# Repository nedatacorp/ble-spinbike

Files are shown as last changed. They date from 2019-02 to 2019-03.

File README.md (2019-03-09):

# ble-spinbike
This project is about building a "smart" spinbike from a low-cost, standard spinbike, thus saving a lot of money and having a lot of fun building it and riding it. The result is a spinbike that will work with popular on-line virtual exercise applications, such as Zwift and Bkool. This project was developed specifically using Zwift, but should work with any other product that supports standard Bluetooth GATT technology.

Spinbike is a Javascript node.js application that runs on a Raspberry Pi 3 B+. It gathers data from sensors attached to a spinbike and feeds the data over a bluetooth LE connection to client applications, using the Bluetooth LE (Low Energy) GATT protocol. The GATT protocol is recognized by all major online virtual exercise platforms.

This project provides three of the main exercise bike services: Cadence/Speed, Power and Control. Online apps generally require at least Cadence/Speed or Power in order to allow you to connect and participate. Control is optional, and generally involves feeding the bike information about wind speed, road resistance and grade so it can adjust the effort required by the rider. You can build as much or as little as you want. 

Here is the fritzing diagram for the Raspberry PI, sensors and controllers:

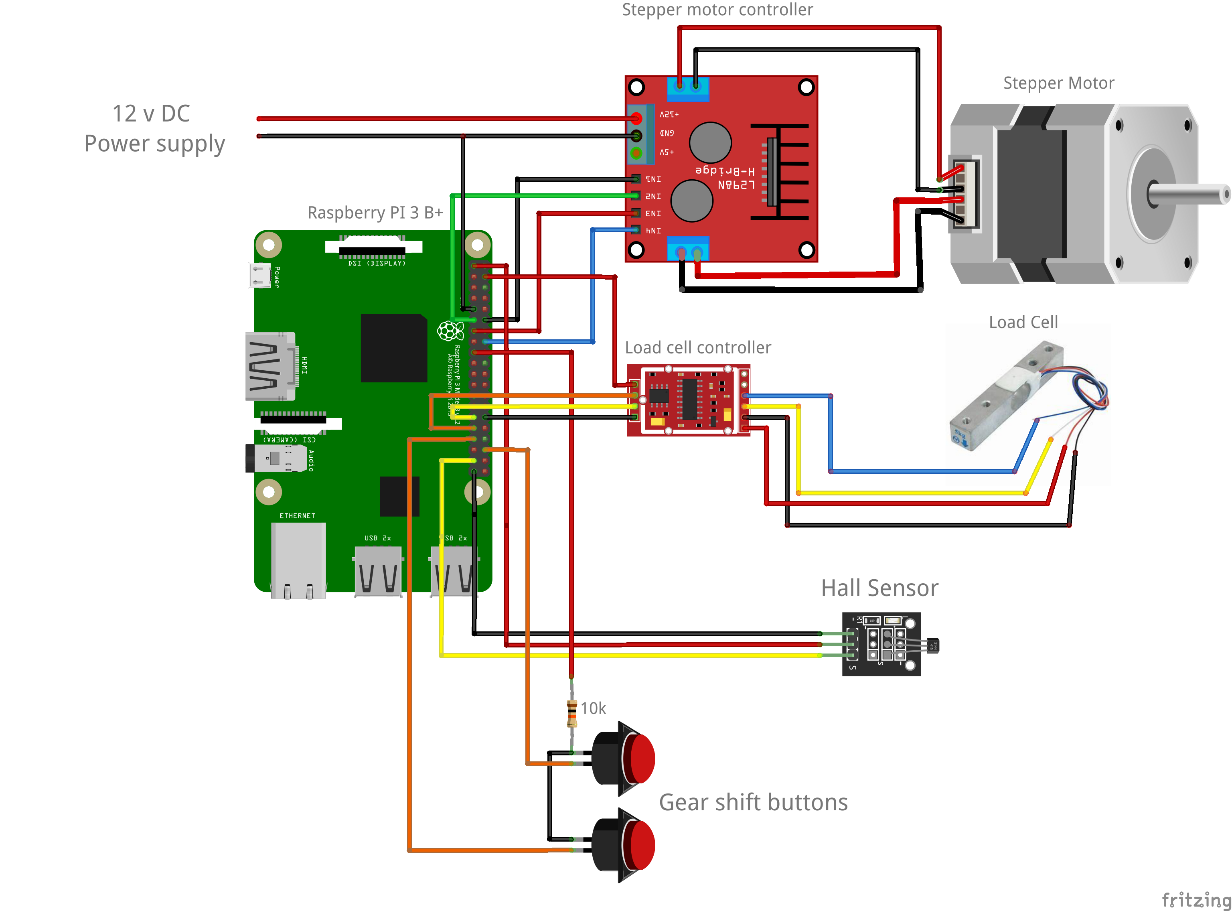
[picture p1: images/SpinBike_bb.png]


I chose a Yosuda spin bike for this project:

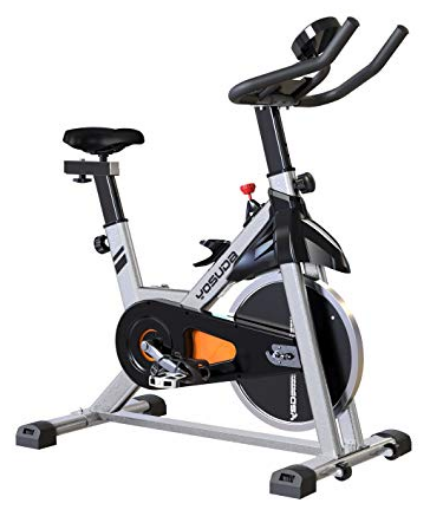
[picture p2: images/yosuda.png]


It has three attributes that make it nice for installing the sensors we need, and the optional stepper motor for controlling resistance:

* A magnet on the main drive pulley and a hole just below the crankshaft where a Hall sensor can be mounted for measuring cadence.
* A steering head that is extended below the main frame, providing a perfect location to mount the load cell for measuring the force on the wool brake pad from the front wheel. 
* A flat-sided steering head and a tension shaft located in just the right spot for making it easy to mount the optional stepper motor, which replaces the tension knob and allows for computerized resistance control.

## System Diagram

This is how the software pieces fit together:

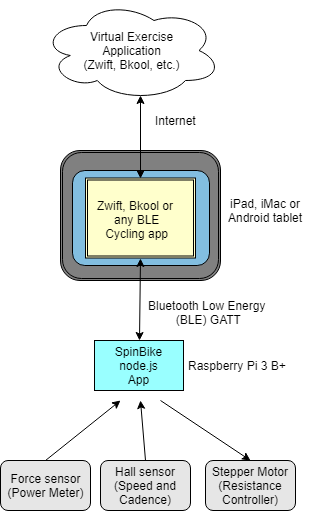
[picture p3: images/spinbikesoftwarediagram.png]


Although most cycling applications support ANT as well as Bluetooth LE (hereafter referred to as "BLE"), I chose Bluetooth for a couple reasons:

* We're using a spinbike, which is indoors and stationary. We don't need the robustness of ANT that's better suited for outdoors and real bicycles. 
* We can use conventional, built-in bluetooth devices, thus avoiding the added cost of ANT dongles.

The major components of this project are the spin bike, a tablet (iPad or Android) or smart phone (iphone or Android), a Raspberry Pi, and about $50 in sensors/misc. hardware. You can also use a standard Mac or PC in place of the tablet, but a tablet works better because you can mount it on the handlebars. You do need either a smart phone/tablet or computer that supports Bluetooth 4.0 and thus Bluetooth low energy. 

Although you don't need the latest computer equipment for this, you also can't use antiques. I specify the Raspberry Pi 3 B+ because it has built-in bluetooth. Old iPads won't run the Zwift app. On the other hand, I had no problem using a 2007 iMac. You'll have to experiment.

For situations where you don't have a tablet that has bluetooth LE capability, you can run a bridge application such as "Zwift Companion" on your smart phone that will communicate between your spin bike (our Raspberry Pi computer, actually) and the full-blown Zwift application running on your PC or Mac.

## Parts List

|Part |Description |Price |Link |
|:--- |:---|:-----|:---|
|L-001A |Yosuda Spin Bike |$250  |https://www.amazon.com/dp/B07D528W98/ref=emc_b_5_t|
|RaspBerry Pi 3 B+|Raspberry Pi|$50|https://www.amazon.com/CanaKit-Raspberry-Power-Supply-Listed/dp/B07BC6WH7V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|
|KY-003 Hall Sensor|Hall Sensor with controller board|$3|https://www.amazon.com/SODIAL-magnetic-sensor-module-Arduino/dp/B077RSV94Z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|
|Flex Coupling|For connecting stepper motor to resistance shaft|$8|https://www.amazon.com/gp/product/B01HBPHSII/ref=ppx_yo_dt_b_asin_title_o07__o00_s00?ie=UTF8&psc=1|
|17HS13-0404S1|Nema 17 stepper motor|$11|https://www.amazon.com/gp/product/B00PNEQ9T4/ref=ppx_yo_dt_b_asin_title_o02__o00_s00?ie=UTF8&psc=1|
|Stepper motor bracket|For attaching stepper motor to steering post|$6.50|https://www.amazon.com/gp/product/B00Q6F51C0/ref=ppx_yo_dt_b_asin_title_o03__o00_s00?ie=UTF8&psc=1|
|L298N|Stepper motor controller|$7|https://www.amazon.com/gp/product/B00CAG6GX2/ref=ppx_yo_dt_b_asin_title_o04__o00_s00?ie=UTF8&psc=1|
|Hx711|Load Cell|$13|https://www.amazon.com/gp/product/B075317R45/ref=ppx_yo_dt_b_asin_title_o05__o00_s00?ie=UTF8&psc=1|
|28 awg 3-conductor wire|3 conductor with ground|$12|https://www.amazon.com/StrivedayTM-3-core-Control-Shielded-Headphone/dp/B01LNH94Y6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|
|12 v power supply|For powering stepper motor|$8|https://www.amazon.com/inShareplus-Mounted-Switching-Connector-Adapter/dp/B01GD4ZQRS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|
|Buttons|Pushbuttons for controlling resistance|$7|https://www.amazon.com/yueton-Momentary-Button-Switch-Toggle/dp/B0119FH5Z2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|
|10k Resistor|You only need 1. You probably have some lying around.|$6|https://www.amazon.com/10k-Carbon-Film-Resistors-Pack/dp/B01NAVJIE1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|

Also:
* Friction tape (works better than plastic electrical tape)
* Duct tape
* iPad or Android tablet
* Keyboard, mouse and monitor for programming Raspberry Pi
* A couple of metal channel brackets and bolts from HD or Lowes for mounting the stepper motor
* Small screws for mounting stepper motor and load cell

## Tools
* Soldering iron
* Rosin-core electical solder
* Small standard and phillips screwdrivers
* Knife and/or wire strippers

# General Procedure

* Configure Raspberry Pi
* Install Spinbike Software
* Connect and test sensors and stepper motor
* Install sensors and stepper hardware to cycle
* Install cycling application
* Test
* Go cycling!

## Configure Raspberry Pi

### Bluetooth Setup

Open a terminal window. Enter the following commands:

1.	sudo systemctl stop bluetooth
2.	sudo systemctl disable bluetooth
3.	sudo systemctl mask bluetooth.service
4.	sudo hciconfig hci0 up   (that’s a zero – not an O)
5.	crontab -e
6.	Add this line:  @reboot sudo -u root hciconfig hci0 up
7.	sudo apt-get install npm
8.	sudo apt-get install bluetooth bluez libbluetooth-dev libudev-dev

## Install Spinbike Software
1.  Open terminal window
2.  cd Desktop
3.  git clone https://github.com/nedatacorp/ble-spinbike.git
4.	cd to the Desktop/ble-spinBike folder
5.  npm install

## Connect and test sensors and stepper motor

The best path to success is to hook up and test each device one at a time, then afer everything is proven to be connected correctly, move the sensors, wiring and other hardware into place for the final assembly and test.

Each device has a JavaScript test script in the Tests folder as well as a Python script in the Python folder that you can use for testing.

### The Load Cell

Mount one end of the load cell to a piece of plywood next to the Pi, using nuts or washers for stand-offs. You need to have some space between the remainder of the load cell and the pywood so you can flex the load cell.

Connect the load cell to the load cell controller, and the load cell controller to the Pi using the Fritzing diagram.

Open a terminal window and cd to the Desktop/ble-spinbike/Tests folder.

Enter:  sudo node forcesensortest.js

You should see the values from the sensor displayed on the screen. If you press on the free end of the load cell, you should see the values increase.

### The Hall Sensor

Wire up the Hall sensor as shown in the Fritzing diagram. Open a terminal window and cd to the Desktop/ble-spinbike/Tests folder.

Enter: sudo node crankspeedtest.js

Pass a magnet close to the transistor on the Hall sensor board. You should see a "Count: " message displayed on the screen, with the number incrementing each time you pass the magnet close to the sensor.

### The stepper Motor

Connect the stepper motor to the stepper motor controller, and the controller to the Pi using the Fritzing diagram as a guide.

Connect a 12v, 2 amp DC power supply to the stepper motor controller and plug it in. The LED on the controller board should light up.

From a terminal window, cd to the Desktop/ble-spinbike/Tests folder.

Enter: sudo node steppertest.js

The stepper motor should run 360 degrees clockwise and then 360 degrees counter-clockwise.

### Shift Buttons   

These are used for adjusting the tension on the wool brake pad that presses on the flywheel to increase or decrease the power you have to apply to the spinbike. They run the stepper motor forward or backward. You will want to mount these buttons in a small case and attach them to the handlebars or some other place that is convenient to reach while cycling. 

Refer to the Fritzing diagram to wire the buttons. 

From a terminal window, cd to the Desktop/ble-spinbike/Tests folder.

Enter: sudo node buttontest.js

Press and release each of the buttons. You should see a message on the screen indicating that you've pressed each button.

## Install hardware on the spinbike

### The Power Sensor

The power sensor is the load-cell. We attach it behind the steering post using two 1/4" nuts as stand-offs. A long 4mm screw with a stop nut on it is installed and adjusted to just touch the front of the plastic brake shoe.

Here is a picture that shows the two large holes drilled into the front of the steering post. The holes need to be large enough for the heads of the two 5mm bolts to pass through:

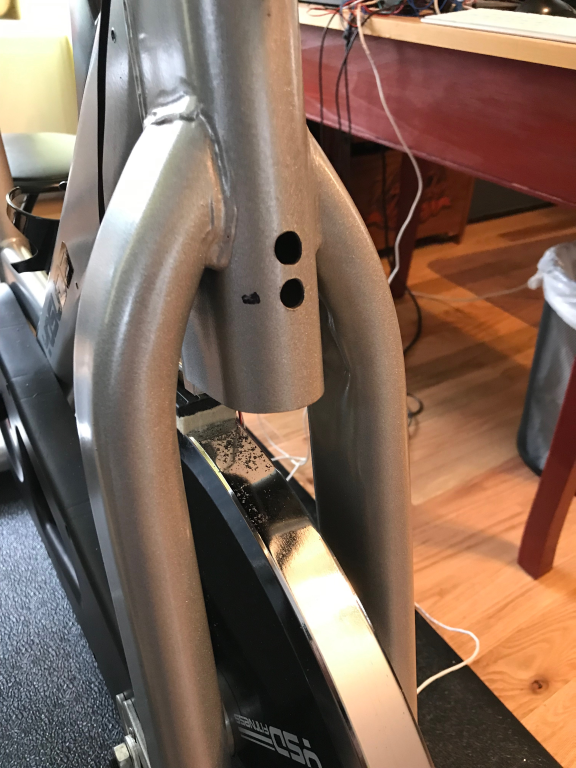
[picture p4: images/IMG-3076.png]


Here is a view from the right side of the bike, showing the load-cell mounted on the steering post:

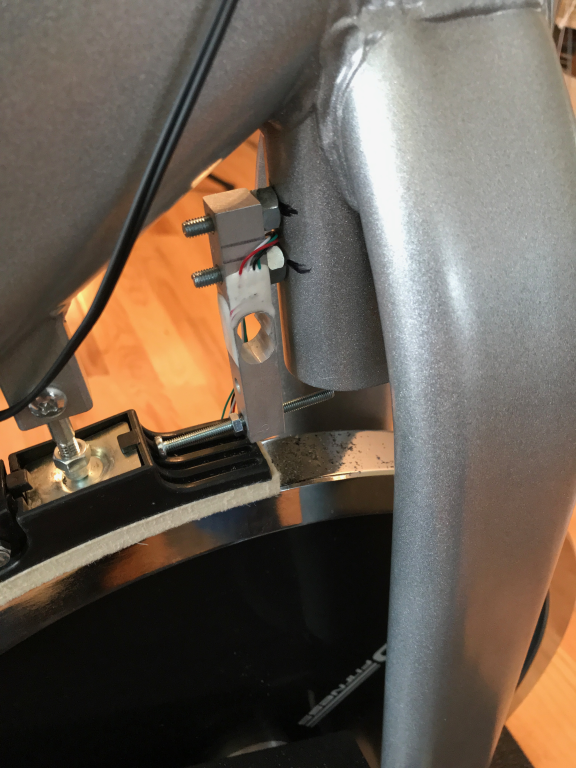
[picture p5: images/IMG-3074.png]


You should also make sure the brake shoe is loose in the metal bracket so it has some freedom to press against the load-cell screw. I remove the rear screw from the brake shoe and filed the holes for the front screw oblong, so the show can float forward and back just a bit.

### The Resistance Adjuster

The stepper motor is use to adjust the resistance on the flywheel. It replaces the manual adjustment knob and provides a way to programatically adjust the resistance. 

First, use a hacksaw to cut the knob off the top of the adjustment shaft (you can remove it from the bike to make that easier), then install the 5 x 8mm flex coupling:

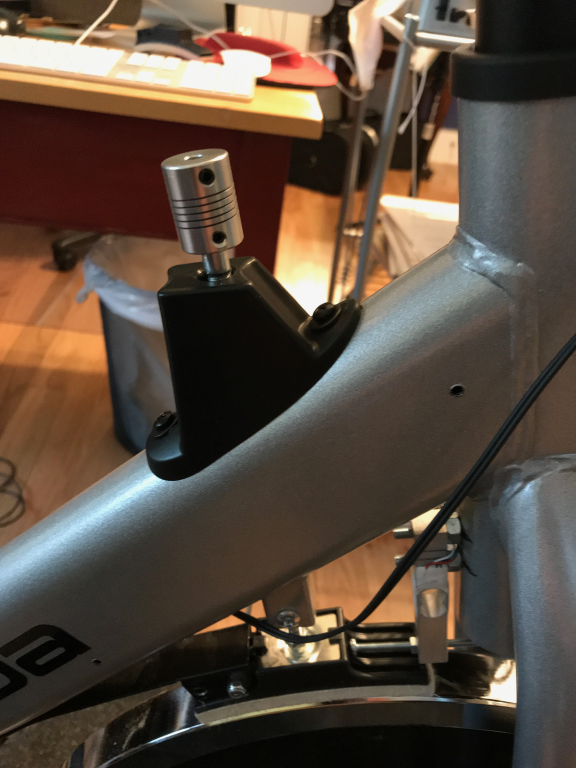
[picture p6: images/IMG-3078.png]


The stepper motor is attached to the coupling and then two metal brackets are used in conjunction with the l-shaped stepper motor bracket to stabilize the stepper motor against the steering post. I used two 1/4" thin pieces of rubber from a mouse pad between the brackets an the steering post to make everything line up:

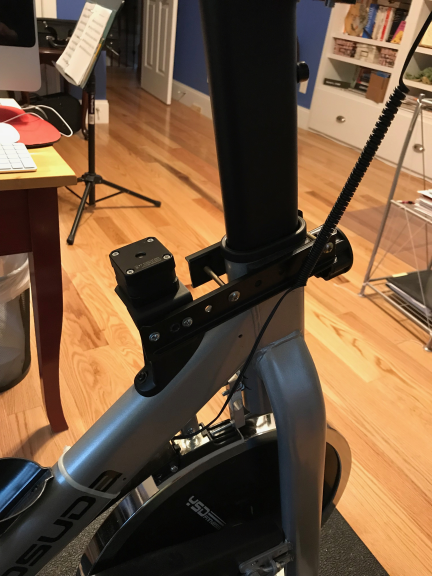
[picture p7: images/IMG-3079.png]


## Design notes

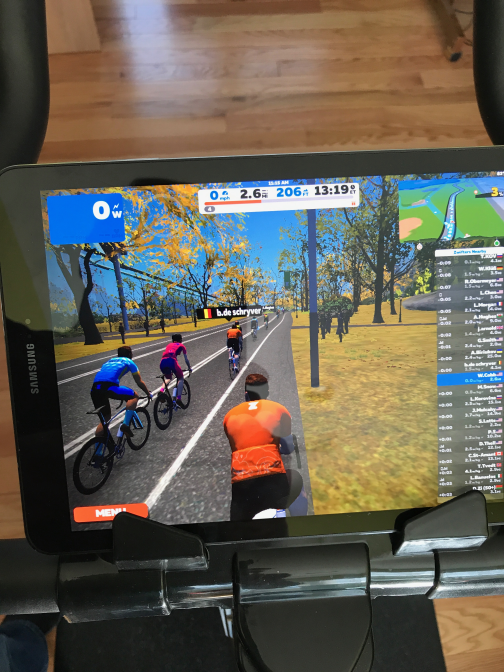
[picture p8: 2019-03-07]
images/zwift.png

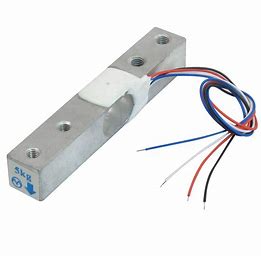
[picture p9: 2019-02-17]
Docs/loadcell.jpg

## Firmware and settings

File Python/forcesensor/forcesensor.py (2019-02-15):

import RPi.GPIO as GPIO
import time
import sys
from hx711 import HX711

def cleanAndExit():
    print "Cleaning..."
    GPIO.cleanup()
    print "Bye!"
    sys.exit()

hx = HX711(5, 6)

z= 104.7371

# I've found out that, for some reason, the order of the bytes is not always the same between versions of python, numpy and the hx711 itself.
# Still need to figure out why does it change.
# If you're experiencing super random values, change these values to MSB or LSB until to get more stable values.
# There is some code below to debug and log the order of the bits and the bytes.
# The first parameter is the order in which the bytes are used to build the "long" value.
# The second paramter is the order of the bits inside each byte.
# According to the HX711 Datasheet, the second parameter is MSB so you shouldn't need to modify it.
hx.set_reading_format("MSB", "MSB")

# HOW TO CALCULATE THE REFFERENCE UNIT
# To set the reference unit to 1. Put 1kg on your sensor or anything you have and know exactly how much it weights.
# In this case, 92 is 1 gram because, with 1 as a reference unit I got numbers near 0 without any weight
# and I got numbers around 184000 when I added 2kg. So, according to the rule of thirds:
# If 2000 grams is 184000 then 1000 grams is 184000 / 2000 = 92.
#hx.set_reference_unit(113)
hx.set_reference_unit(80000)

hx.reset()
#hx.tare()

# to use both channels, you'll need to tare them both
#hx.tare_A()
#hx.tare_B()


while True:
    try:
        # These three lines are useful to debug wether to use MSB or LSB in the reading formats
        # for the first parameter of "hx.set_reading_format("LSB", "MSB")".
        # Comment the two lines "val = hx.get_weight(5)" and "print val" and uncomment the three lines to see what it prints.
        #np_arr8_string = hx.get_np_arr8_string()
        #binary_string = hx.get_binary_string()
        #print binary_string + " " + np_arr8_string
        
        # Prints the weight. Comment if you're debugging the MSB and LSB issue.
        val = hx.get_weight(5) + z
        val = val  * 100
    #val = hx.read_long()
        print val

        # To get weight from both channels (if you have load cells hooked up 
        # to both channel A and B), do something like this
        #val_A = hx.get_weight_A(5)
        #val_B = hx.get_weight_B(5)
        #print "A: %s  B: %s" % ( val_A, val_B )

        hx.power_down()
        hx.power_up()
        time.sleep(0.1)
    except (KeyboardInterrupt, SystemExit):  
        cleanAndExit()

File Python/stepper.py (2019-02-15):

import RPi.GPIO as GPIO
from time import sleep
import sys

#12 = IN1  - On 1 & 4, we get 3v, 0 on 2 and 3
#11 = IN2  - On 2 & 3, we get 3v, 0 on 1 and 4
#13 = IN3  - On 1 & 2m we get 3v, 0 on 3 and 4
#16 = IN4  - 0 all the time
#assign GPIO pins for motor

motor_channel = (12,13,11,16)
 
GPIO.setwarnings(False)
GPIO.setmode(GPIO.BOARD)
#for defining more than 1 GPIO channel as input/output use
GPIO.setup(motor_channel, GPIO.OUT)

motor_direction = raw_input('select motor direction a=anticlockwise, c=clockwise: ')

print('motor direction: ' + motor_direction)

while True:
    try:
        if(motor_direction == 'c'):
            print('motor running clockwise\n')
            GPIO.output(motor_channel, (GPIO.HIGH,GPIO.HIGH,GPIO.LOW,GPIO.LOW))
            sleep(0.02) 
            GPIO.output(motor_channel, (GPIO.LOW,GPIO.HIGH,GPIO.HIGH,GPIO.LOW))
            sleep(0.02)  
            GPIO.output(motor_channel, (GPIO.LOW,GPIO.LOW,GPIO.HIGH,GPIO.HIGH))
            sleep(0.02) 
            GPIO.output(motor_channel, (GPIO.HIGH,GPIO.LOW,GPIO.LOW,GPIO.HIGH))
            sleep(0.02)   

        elif(motor_direction == 'a'):
            print('motor running anti-clockwise\n')
            GPIO.output(motor_channel, (GPIO.HIGH,GPIO.LOW,GPIO.LOW,GPIO.HIGH))
            sleep(0.02)
            GPIO.output(motor_channel, (GPIO.LOW,GPIO.LOW,GPIO.HIGH,GPIO.HIGH))
            sleep(0.02)
            GPIO.output(motor_channel, (GPIO.LOW,GPIO.HIGH,GPIO.HIGH,GPIO.LOW))
            sleep(0.02)
            GPIO.output(motor_channel, (GPIO.HIGH,GPIO.HIGH,GPIO.LOW,GPIO.LOW))
            sleep(0.02)

            
    #press ctrl+c for keyboard interrupt
    except KeyboardInterrupt:
        #query for setting motor direction or exit
        motor_direction = raw_input('select motor direction a=anticlockwise, c=clockwise or q=exit: ')
        #check for exit
        if(motor_direction == 'q'):
            print('motor stopped')
            sys.exit(0)
 

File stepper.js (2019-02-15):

var GPIO = require('onoff').Gpio; //include onoff to interact with the GPIO
var sleep = require('sleep');

class Stepper {
  
  constructor(sensorpins)
  { 
    this.IN1 = new GPIO(sensorpins[0], 'out');
    this.IN2 = new GPIO(sensorpins[1], 'out');
    this.IN3 = new GPIO(sensorpins[2], 'out');
    this.IN4 = new GPIO(sensorpins[3], 'out'); 
    
    this.forward = [[1,1,0,0],
                    [0,1,1,0],
                    [0,0,1,1],
                    [1,0,0,1]];
                    
     this.curstep = 0;             
                               
  }
  
  //Rotate clockwise
  stepc (count, pause) {
    if (pause<1)
      pause = 1;
 
 
    for (var c = 0; c < count; c++)
    {
        this.curstep +=1;
        if (this.curstep>3)
          this.curstep = 0;      
        this.IN1.writeSync(this.forward[0][this.curstep]);
        this.IN2.writeSync(this.forward[1][this.curstep]);
        this.IN3.writeSync(this.forward[2][this.curstep]);
        this.IN4.writeSync(this.forward[3][this.curstep]);
        if (pause>0)
          sleep.msleep(pause);
    }
  }
  
  //Rotate counter-clockwise
  stepcc (count, pause) {
    if (pause<1)
      pause = 1;

    for (var c = 0; c < count; c++)
    {
        this.curstep = this.curstep-1;
        if (this.curstep<0)
           this.curstep = 3;     
        this.IN1.writeSync(this.forward[0][this.curstep]);
        this.IN2.writeSync(this.forward[1][this.curstep]);
        this.IN3.writeSync(this.forward[2][this.curstep]);
        this.IN4.writeSync(this.forward[3][this.curstep]);
        if (pause>0)
          sleep.msleep(pause);
    }   
  }
  
  //This turns off the the power to all coils to avoid heat build-up. However, this allows the
  // motor shaft to turn easily, so don't call this if you want the motor to hold position.
  cool () {
    this.IN1.writeSync(0);
    this.IN2.writeSync(0);
    this.IN3.writeSync(0);
    this.IN4.writeSync(0);   
  }
}

module.exports.Stepper = Stepper;

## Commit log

2019-02-17 Added fritzing diagram
    [SpinBike.fzz]
2019-02-23 Added handling of shifter buttons
2019-02-24 Updated readme.md with shift buttons
